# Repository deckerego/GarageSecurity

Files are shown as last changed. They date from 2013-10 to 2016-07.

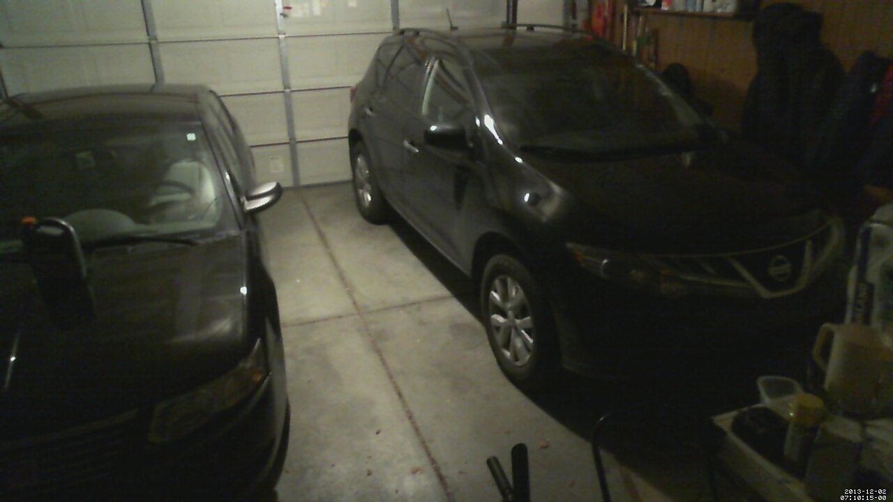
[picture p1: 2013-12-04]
app/test/unit/two_cars_closed_nightlight.jpg

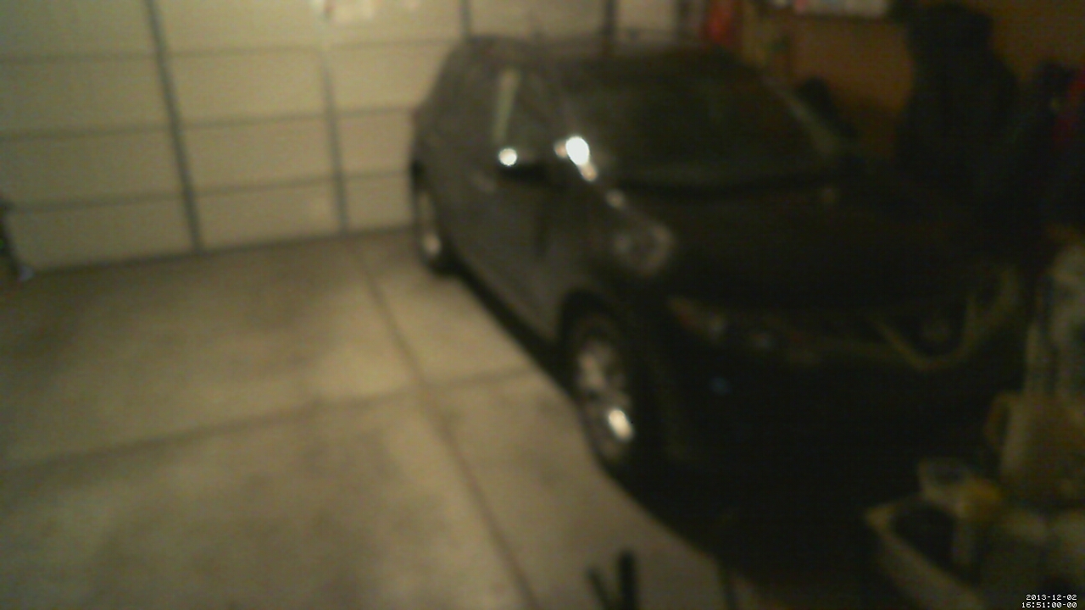
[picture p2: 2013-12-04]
app/test/unit/one_car_closed_nightlight.jpg

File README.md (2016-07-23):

GarageSecurity
==============

A web interface for remote residential garage surveillance. This uses a Raspberry Pi to connect to a universal garage door opener via GPIO and a webcam or Raspberry NoIR video camera.

Hardware Punch List
-------------------

<table>
  <tr>
    <td>Raspberry Pi (works with all models)</td>
    <td>https://www.adafruit.com/product/2266</td>
  </tr>
  <tr>
    <td>Raspberry Pi NoIR Camera (or a spare Video4Linux-compliant webcam)</td>
    <td>https://www.sparkfun.com/products/12654</td>
  </tr>
  <tr>
    <td>Chamberlain Universal Garage Remote</td>
    <td>http://www.chamberlain.com/clicker-and-accessories/universal-clicker-products/clicker-universal-remote-control</td>
  </tr>
  <tr>
    <td>Resistors, NPN transistors, NPN MOSFET</td>
    <td>Available at Sparkfun, Adafruit, Radio Shack or from de-soldering unused electronics.</td>
  </tr>
  <tr>
    <td>Optional: Honeywell Temperature and Humidity Sensor</td>
    <td>https://www.sparkfun.com/products/11295</td>
  </tr>
</table>

Security & OS Setup
-------------------

Ensure you install necessary updates and install a firewall (such as UFW) before proceeding. Rather than exposing motion and other services externally, we will be proxying them through Apache. This means the only ports you should need to open are port 80 (HTTP) and port 22 (SSH), especially since motion hasn't has as extensive vetting for security. As an example, you could setup a simple firewall as:
~~~~
sudo apt-get install ufw
sudo ufw allow 80
sudo ufw allow 22
sudo ufw enable
~~~~
Bear in mind GarageSec uses BASIC HTTP authentication and does not necessarily support SSL out of the box (although you could definitely add it), so man-in-the-middle interception of your password is super-de-duper possible.

Also - the latest version of Raspian (Jessie) doesn't bring up wireless interfaces on boot by default, even for the RPi 3. Which is odd. To fix this, make sure your wireless interfaces in `/etc/network/interfaces` are set to "auto," such as:
~~~~
auto wlan0
allow-hotplug wlan0
iface wlan0 inet manual
    wpa-conf /etc/wpa_supplicant/wpa_supplicant.conf
~~~~

It may be a good idea to create a crontab entry to delete old captured videos, e.g. `0 1 * * * find /home/motion -ctime +14 -delete`

To enable I2C communication for temperature and humidity monitoring, follow the I2C instructions from Adafruit available at https://learn.adafruit.com/adafruits-raspberry-pi-lesson-4-gpio-setup/configuring-i2c

Hardware Installation
---------------------

See http://hackaday.io/project/2049/instructions for hardware installation

Software Installation
---------------------

These installation instructions have been tested with the latest version of Raspian (Jessie)

1. Install the base packages with `sudo apt-get install wiringpi python-dev python-smbus python-imaging apache2 libapache2-mod-proxy-html libapache2-mod-authnz-external motion nodejs-legacy libav-tools npm monit`
2. Install Bower using `sudo npm install -g bower`
3. Enable the Apache2 modules using `sudo a2enmod authnz_external proxy_http`
4. If you are using the Raspberry Pi camera, add `bcm2835-v4l2` to /etc/modules
5. Edit `/etc/default/motion` and set it to start on boot
6. Clone this repository or download https://github.com/deckerego/GarageSecurity/archive/master.zip which will include the Bottle webapp and some admin configs/scripts
7. Install GarageSecurity's dependencies using `sudo pip install -r app/requirements.txt`
8. Expose any GPIO ports you connect the garage door opener or light switches using the WiringPi GPIO Utility, e.g. `gpio export 17 out`. You may want to add this statement to `/etc/rc.local` so that it will be exported at startup. A sample rc.local is provided.
9. Allow the pi user to access motion files by adding it to the `motion` user group in /etc/group
10. Copy the files within the app/ directory into /srv/garagesec
11. Change into the /srv/garagesec/views directory and execute `bower install bootstrap`
12. Copy the service config files from config/etc into the appropriate /etc directory, altering them as needed.
13. Copy the alert scripts from the `scripts/` directory into `/usr/local/motion`, modifying `rest_call.sh` so that API_USER and API_PASS are set to your "pi" usernamed and password used to log in to Apache
14. Create a copy of app/config.sample as /srv/garagesec/config.py, altering config.py to fit your preferences
15. Enable the webapp with `sudo a2dissite 000-default`, followed by `sudo a2ensite security`, then start up (or restart) Apache2
16. Ensure config/etc/init.d/garagesec has been copied to /etc/init.d, then install it using `sudo update-rc.d garagesec defaults`
17. Start the webapp using `sudo service garagesec start`

GPIO Permissions Issues
-----------------------
You may find that the GPIO buttons don't work as expected - this may be due to permissions issues within the `/sys/class/gpio/` devices. This can sometimes be fixed by changing `/etc/udev/rules.d/99-com.rules` to have the following gpio rules: `SUBSYSTEM=="gpio*", PROGRAM="/bin/sh -c 'chown -H -R root:gpio /sys/class/gpio/* && chmod -R 770 /sys/class/gpio/*; chown -R root:gpio /sys/devices/virtual/gpio && chmod -R 770 /sys/devices/virtual/gpio'"`

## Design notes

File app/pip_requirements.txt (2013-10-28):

bottle==0.11.6
nose>=1.1.2
flexmock==0.9.7
wiringpi>=1.0.5

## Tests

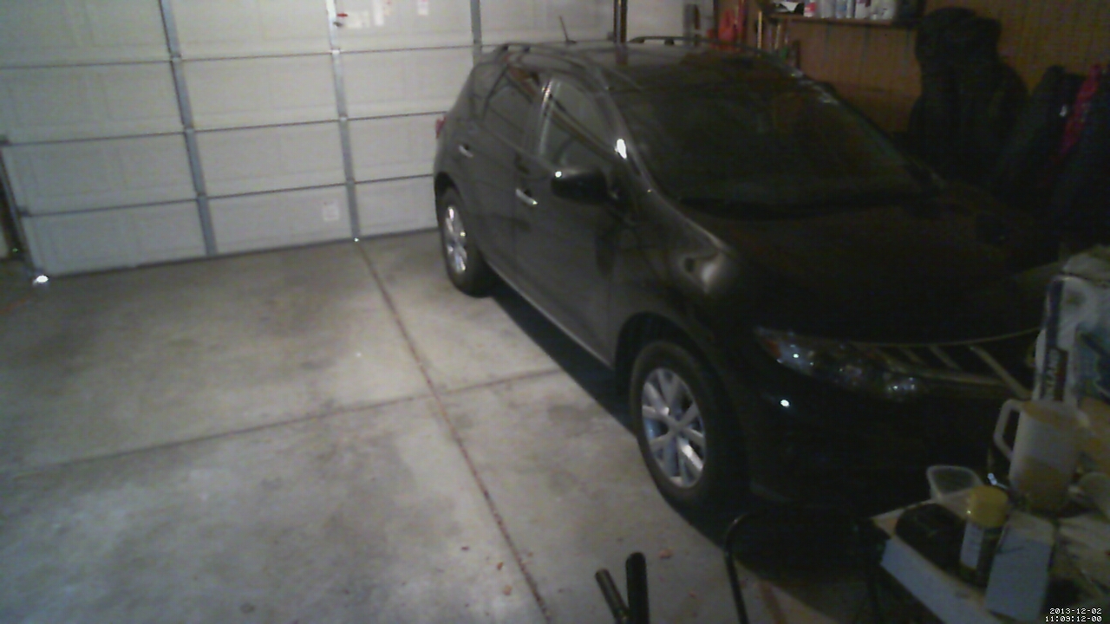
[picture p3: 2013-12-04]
app/test/unit/one_car_closed_day.jpg

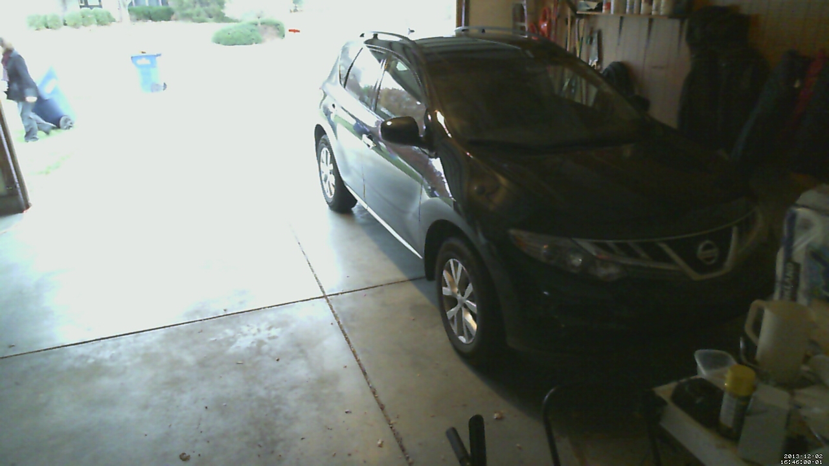
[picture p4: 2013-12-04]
app/test/unit/one_car_open_day.jpg

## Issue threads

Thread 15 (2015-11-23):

2 door setup

kfakhri1, 2015-11-23:
Hi, thanks for posting this, any way this could be configured for two door garages?  As in left door and right door?  Thank you.

deckerego, 2016-04-20:
Yup, that's a doable thing - will look into that.

DervMan, 2016-04-21:
As a variation to that, my door uses a separate button for open and close so I also need two buttons but for a slightly different reason!

DervMan, 2017-01-18:
I've treid to add a second button, in my case I'm after an 'Open' and 'Close'. Although the code below adds the button clicking the new button results in the 'Open button' relay being operated.  Assuming I need to update some more code by struggling to see where.

`<li><button type="button" id="openDoor" class="btn btn-default navbar-btn" onClick="executeCommand();">Open</button></li>
					<li><button type="button" id="closeDoor" class="btn btn-default navbar-btn" onClick="executeCommand();">Close</button></li>`

deckerego, 2017-01-19:
You would need two different JavaScript functions to call - one to open, another to close. Take a look at `events.js` - it has a function called `executeCommand()` that calls `remote/0`. To add a second button, you would need:
1. A new REST endpoint like `remote/` that would trigger a new GPIO pin
2. A new JavaScript function that called this REST endpoint
3. The new button on the UI

deckerego, 2017-01-20:
@DervMan and @kfakhri1 - long at last I have a test out that you guys might try. I've labelled two buttons "Open/Close Door #1" and "Open/Close Door #2," but those are temporary labels for now. This _should_ allow you to fire two different buttons: one on GPIO #17, the other on GPIO #27.

You may even want to just fork the branch `double_button` - if it doesn't work, it should be pretty dang close. Let me know if either of you have success!

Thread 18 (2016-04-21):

Camera0 URL on main page is a static URL

DervMan, 2016-04-21:
When accessing GarageSec main page on anything other than port 80 the camera stream is broken. This link needs to be created dynamically so TCP port changes don't break the URL.

		<script src="installed/jquery/dist/jquery.min.js"></script>
		<script src="installed/bootstrap/dist/js/bootstrap.min.js"></script>
		<script type="text/javascript" src="js/mjpeg_viewer.js"></script>
		<script type="text/javascript" src="js/events.js"></script>
		<script type="text/javascript">
			loadThermals("temperature", "humidity")
			renderCamera("camera0", "http://10.10.10.10/camera0");
			silenceStatus("silent");
			lastEvent("lastevent")
		</script>

deckerego, 2016-07-19:
Implemented as a config change

Closed 2016-07-19.

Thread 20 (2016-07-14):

GarageSecurity not starting up -

DervMan, 2016-07-14:
When trying to open the door I'm seeing a wiringpi GPIO error. Version  WebIOPi-0.7.1.

`root@raspberrypi:/srv/garagesec# python run_server.py
Bottle v0.12.9 server starting up (using WSGIRefServer())...
Listening on http://localhost:9003/
Hit Ctrl-C to quit.

127.0.0.1 - - [14/Jul/2016 12:33:12] "GET / HTTP/1.1" 200 2229
127.0.0.1 - - [14/Jul/2016 12:33:14] "GET /installed/bootstrap/dist/css/bootstrap.min.css HTTP/1.1" 304 0
127.0.0.1 - - [14/Jul/2016 12:33:14] "GET /installed/bootstrap/dist/js/bootstrap.min.js HTTP/1.1" 304 0
127.0.0.1 - - [14/Jul/2016 12:33:14] "GET /installed/jquery/dist/jquery.min.js HTTP/1.1" 304 0
127.0.0.1 - - [14/Jul/2016 12:33:14] "GET /css/styles.css HTTP/1.1" 304 0
127.0.0.1 - - [14/Jul/2016 12:33:14] "GET /js/mjpeg_viewer.js HTTP/1.1" 304 0
127.0.0.1 - - [14/Jul/2016 12:33:14] "GET /installed/bootstrap/dist/css/bootstrap-theme.min.css HTTP/1.1" 304 0
127.0.0.1 - - [14/Jul/2016 12:33:15] "GET /js/events.js HTTP/1.1" 304 0
Traceback (most recent call last):
  File "/usr/local/lib/python2.7/dist-packages/bottle.py", line 862, in _handle
    return route.call(**args)
  File "/usr/local/lib/python2.7/dist-packages/bottle.py", line 1732, in wrapper
    rv = callback(*a, **ka)
  File "/srv/garagesec/HIH6130.py", line 53, in wrapper
    rv = callback(*args, **kwargs)
  File "/srv/garagesec/routes.py", line 86, in get_environment
    humidity, celsius, status = temperature.get_conditions()
  File "/srv/garagesec/HIH6130.py", line 65, in get_conditions
    self.bus.write_quick(self.address)
IOError: [Errno 110] Connection timed out
127.0.0.1 - - [14/Jul/2016 12:33:18] "GET /environment HTTP/1.1" 500 751
Traceback (most recent call last):
  File "/usr/local/lib/python2.7/dist-packages/bottle.py", line 862, in _handle
    return route.call(**args)
  File "/usr/local/lib/python2.7/dist-packages/bottle.py", line 1732, in wrapper
    rv = callback(*a, **ka)
TypeError: get_lastevent() takes exactly 1 argument (0 given)
127.0.0.1 - - [14/Jul/2016 12:33:18] "GET /lastevent HTTP/1.1" 500 749
Traceback (most recent call last):
  File "/usr/local/lib/python2.7/dist-packages/bottle.py", line 862, in _handle
    return route.call(**args)
  File "/usr/local/lib/python2.7/dist-packages/bottle.py", line 1732, in wrapper
    rv = callback(*a, **ka)
TypeError: get_silence() takes exactly 1 argument (0 given)
127.0.0.1 - - [14/Jul/2016 12:33:18] "GET /alerts HTTP/1.1" 500 746
Traceback (most recent call last):
  File "/usr/local/lib/python2.7/dist-packages/bottle.py", line 862, in _handle
    return route.call(**args)
  File "/usr/local/lib/python2.7/dist-packages/bottle.py", line 1732, in wrapper
    rv = callback(*a, **ka)
  File "/srv/garagesec/routes.py", line 149, in read_light_switch
    state = "true" if gpio.read_switch(switch) else "false"
  File "/srv/garagesec/gpio.py", line 38, in read_switch
    **io = wiringpi.GPIO(wiringpi.GPIO.WPI_MODE_SYS)**
AttributeError: type object 'GPIO' has no attribute 'WPI_MODE_SYS'
127.0.0.1 - - [14/Jul/2016 12:33:18] "GET /light/0 HTTP/1.1" 500 747
127.0.0.1 - - [14/Jul/2016 12:33:18] "GET /favicon.ico HTTP/1.1" 200 2686

`

deckerego, 2016-07-19:
Will work on converting the project to the latest build of Raspian

deckerego, 2016-07-22:
I was unable to reproduce on a brand-new build from master using the latest from Raspian. Can you confirm you are running the latest?

Closed 2016-07-23.

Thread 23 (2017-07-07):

Service Unavailable

wjstone, 2017-07-07:
I've tried installing several times and keep ending up getting
"Service Unavailable

The server is temporarily unable to service your request due to maintenance downtime or capacity problems. Please try again later."

any ideas what might be causing it?

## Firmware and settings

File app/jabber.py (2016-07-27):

import sleekxmpp
import inspect
import logging
import datetime
import os, time
from s3 import S3
from camera import Camera
from config import configuration

logger = logging.getLogger('garagesec')
logger.setLevel(20)

class Jabber(sleekxmpp.ClientXMPP):
  name = 'jabber_xmpp'
  keyword = 'jabber'

  def __init__(self, jid, password, camera, temperature):
    super(Jabber, self).__init__(jid, password)

    self.camera = camera
    self.temperature = temperature
    self.instance_name = configuration.get('instance_name').lower()
    self.silent = True

    if jid and password:
        self.silent = False
        self.add_event_handler('session_start', self.start, threaded=False, disposable=True)
        self.add_event_handler('message', self.receive, threaded=True, disposable=False)

  def __del__(self):
    self.close()

  # This is invoked when installed as a Bottle plugin
  def setup(self, app):
    self.routes = app

    for other in app.plugins:
      if not isinstance(other, Jabber):
        continue
      if other.keyword == self.keyword:
        raise PluginError("Found another instance of Jabber running!")

    host = configuration.get('xmpp_server_host')
    port = configuration.get('xmpp_server_port')

    if not host or not port:
        logger.warn("No XMPP settings defined, disabling Jabber")
    else:
        if self.connect((host, port)):
          logger.info("Opened XMPP Connection")
          self.process(block=False)
        else:
          raise Exception("Unable to connect to Google Jabber server")

        self.bucket = S3()

  # This is invoked within Bottle as part of each route when installed
  def apply(self, callback, context):
    conf = context.config.get('jabber') or {}
    keyword = conf.get('keyword', self.keyword)

    args = inspect.getargspec(context.callback)[0]
    if keyword not in args:
      return callback

    def wrapper(*args, **kwargs):
      kwargs[self.keyword] = self
      rv = callback(*args, **kwargs)
      return rv
    return wrapper

  # De-installation from Bottle as a plugin
  def close(self):
    logger.info("Closing XMPP Connection")
    self.disconnect(wait=False)

  def start(self, event):
    self.send_presence()
    self.get_roster()

  def send_alert_image(self, file_path):
    if not self.silent:
      file_bin = open(file_path, 'r').read()
      file_url = self.bucket.upload(file_bin)
      self.send_alert_msg(file_url)

  def send_alert_msg(self, body):
    if not self.silent:
        for recipient in configuration.get('xmpp_recipients'):
          message = self.Message()
          message['to'] = recipient
          message['type'] = 'chat'
          message['body'] = body

          logger.debug("Sending message: %s" % message)
          message.send()

  def set_silence(self, silent):
      self.silent = silent

  def receive(self, message):
    if message['type'] in ('chat', 'normal'):
      logger.debug("XMPP Message: %s" % message)
      from_account = "%s@%s" % (message['from'].user, message['from'].domain)
      logger.info("Received message from %s" % from_account)

      if not from_account in configuration.get('xmpp_recipients'):
        logger.warn("Received message from non-whitelist user %s: %s" % (from_account, message['body']))
      elif "%s camera" % self.instance_name in message['body'].lower():
        image_bin = self.camera.get_image()
        image_url = self.bucket.upload(image_bin)
        message.reply("Status: %s" % image_url).send()
      elif "%s lastevent" % self.instance_name in message['body'].lower():
        archive_dir = configuration.get('webcam_archive')
        time_struct = max(map(lambda x: os.path.getmtime("%s/%s" % (archive_dir, x)), os.listdir(archive_dir)))
        message.reply("Last Event: %s" % time.strftime("%c", time.localtime(time_struct))).send()
      elif "%s climate" % self.instance_name in message['body'].lower():
        humidity, celsius, status = self.temperature.get_conditions()
        farenheit = ((celsius * 9) / 5) + 32
        message.reply("Temperature: %0.2fF, Humidity: %0.2f%%" % (farenheit, humidity)).send()
      elif "%s silent" % self.instance_name in message['body'].lower():
        self.silent = True
        message.reply("Silencing alerts").send()
      elif "%s audible" % self.instance_name in message['body'].lower():
        self.silent = False
        message.reply("Enabling alerts").send()
      else:
        logger.info("Uncaught command from %s: %s" % (from_account, message['body']))

class PluginError(Exception):
  pass

Plugin = Jabber

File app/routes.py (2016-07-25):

#!/usr/bin/env python
# -*- coding: utf-8 -*-

import os, sys
import logging

logging.basicConfig(level=logging.WARN, format='%(levelname)-8s %(message)s')
logger = logging.getLogger('garagesec')

os.chdir(os.path.dirname(__file__))
sys.path.insert(0, os.path.abspath(os.path.join(os.path.dirname(__file__), ".")))

import json
import time, datetime
import re
from piwiring import GPIO
from jabber import Jabber
from camera import Camera
from HIH6130 import Temperature
from media import Media
from config import configuration
from bottle import Bottle, HTTPResponse, static_file, get, put, request, response, template, redirect

instance_name = configuration.get('instance_name')

camera = Camera()
temperature = Temperature()
gpio = GPIO()
jabber_service = Jabber(configuration.get('xmpp_username'), configuration.get('xmpp_password'), camera, temperature)
media = Media()

application = Bottle()
application.install(temperature)
application.install(gpio)
application.install(jabber_service)
application.install(media)

@application.route('/favicon.ico')
def send_favicon():
	return static_file('favicon.ico', root='views/images')

@application.route('/installed/<filename:path>')
def send_bower(filename):
	return static_file(filename, root='views/bower_components')

@application.route('/js/<filename:path>')
def send_js(filename):
	return static_file(filename, root='views/js')

@application.route('/css/<filename:path>')
def send_css(filename):
	return static_file(filename, root='views/css')

@application.get('/')
def index():
	return home()

@application.get('/home')
def home():
	return template('index', webcam_url=configuration.get('webcam_url'))

@application.get('/archive')
def archive(media):
	archive_dates = media.get_dates()
	archive_date = request.query.date
	if not (archive_date and media.is_valid_date(archive_date)):
		archive_date = archive_dates[0]

	image_files = media.get_files(archive_date)
	return template('media', images=image_files, date=archive_date, dates=archive_dates)

@application.get('/video')
def video(media):
	video_file = request.query.vid
	archive_date = request.query.date

	if (not media.is_valid_date(archive_date)) or (not media.is_valid_video(video_file)):
		return archive(media)

	return template('video', archive_video=video_file, date=archive_date)

@application.get('/status')
def show_status():
	archive_dir = configuration.get('webcam_archive')
	archive_dir = configuration.get('webcam_archive')
	time_struct = max(map(lambda x: os.path.getmtime("%s/%s" % (archive_dir, x)), os.listdir(archive_dir)))
	return '{ "last_area_detected": "%s" }' % time.strftime("%c", time.localtime(time_struct))

@application.get('/environment')
def get_environment(temperature):
	humidity, celsius, status = temperature.get_conditions()
	fahrenheit_val = ((celsius * 9) / 5) + 32 if celsius else "null"
	celsius_val = celsius if celsius else "null"
	humidity_val = humidity if humidity else "null"
	status_val = status if status else "null"
	return '{ "relative_humidity": %s, "celsius": %s, "fahrenheit": %s, "status": %s }' % (humidity_val, celsius_val, fahrenheit_val, status_val)

@application.get('/snapshot')
def show_snapshot():
	response.headers['Content-Type'] = 'image/jpeg'
	return camera.get_image()

@application.put('/picture_save')
def picture_save(jabber, media):
	motion_event = request.json
	image_file_path = motion_event['file']
	image_file_dir = os.path.dirname(image_file_path)

	jabber.send_alert_image(image_file_path)

	if image_file_dir.index(configuration.get('webcam_archive')) == 0:
		media.save_thumbnail(image_file_path)

	return request.body.getvalue()

@application.put('/movie_start')
def movie_start():
	return request.body.getvalue()

@application.put('/movie_end')
def movie_end(media):
	motion_event = request.json
	video_file_path = motion_event['file']
	video_file_dir = os.path.dirname(video_file_path)

	if video_file_dir.index(configuration.get('webcam_archive')) == 0:
		media.transcode(video_file_path)

	return request.body.getvalue()

@application.put('/motion_detected')
def motion_detected():
	return request.body.getvalue()

@application.put('/area_detected')
def area_detected(jabber):
	motion_event = request.json
	date_time = time.localtime(motion_event['event_time'])
	time_string = time.strftime('%a, %d %b %Y %H:%M:%S', date_time)

	jabber.send_alert_msg('Motion in %s Detected at %s' % (instance_name, time_string))

	return request.body.getvalue()

@application.put('/remote/<button:int>')
def push_remote_button(button, gpio):
	if gpio.push_button(button):
		return '{ "pressed": %d }' % button
	else:
		raise HTTPResponse('{ "error": %d }' % button, 500)

@application.get('/light/<switch:int>')
def read_light_switch(switch, gpio):
	state = "true" if gpio.read_switch(switch) else "false"
	return '{ "enabled": %s }' % state

@application.put('/light/<switch:int>')
def flip_light_switch(switch, gpio):
	if gpio.flip_switch(switch):
		return '{ "flipped": %d }' % switch
	else:
		raise HTTPResponse('{ "error": %d }' % switch, 500)

@application.get('/lastevent')
def get_lastevent(jabber):
	archive_dir = configuration.get('webcam_archive')
	time_struct = max(map(lambda x: os.path.getmtime("%s/%s" % (archive_dir, x)), os.listdir(archive_dir)))
	return '{ "datetime": "%s" }' % time.strftime("%c", time.localtime(time_struct))

@application.get('/alerts')
def get_silence(jabber):
	return '{ "silence": %s }' % ("true" if jabber.silent else "false")

@application.put('/alerts')
def set_silence(jabber):
	silence_request = request.json
	jabber.set_silence(silence_request['silence'])
	return get_silence(jabber)

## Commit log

2013-10-26 Fire the GPIO pin for the door remote
2013-10-30 Switched to Skeleton CSS for reactive design
2013-10-30 Revert "Switched to Skeleton CSS for reactive design"
    This reverts commit 14dd4567be4e7c3347d3f2648352f98507370559.
    [routes.py]
2013-11-27 Issue #3 Issue #4 - Initial addition of XMPP for notifications; REST exposure
    [jabber.py, routes.py]
2013-11-27 Issue #3 - Implemented XMPP messages
    [jabber.py, routes.py]
2013-12-10 Fixed typo in last event date
    [jabber.py, routes.py]
2014-09-05 Better Jabber integration, error handlng improvements
    [jabber.py, routes.py]
2014-12-28 Added in temperature/humidity support via HIH6130
2014-12-29 Fixed typos for lastevent
    [jabber.py]
2015-01-13 Continue bravely on if I2C does not work
    [HIH6130.py]
2015-01-23 Safe failure when i2c fails
    [HIH6130.py, routes.py]
2015-08-15 Additional Monit configs, cleanup, added wiring diagram for GPIO switches
    [GPIO Switches.fzz]
2015-08-22 Cleanup and path fixes
    Relative pathing and bug fixes
    [GPIO Switches.fzz]
2015-09-05 Documentation Cleanup
    Added Bootstrap installation and removed extraneous Camera reference in
    Jabber
2015-09-07 Jabber cleanup
    Cleanup of Jabber threading
2015-09-21 Video archive page
    more-or-less completed video archive page that doesn’t require Apache
    indexes
    [media.py, routes.py]
2015-09-22 Removed index pages, fixed thumbnail sorting
    Removed index pages for GarageSec media since it’s native to the app
    now; fixed thumbnail sorting
    [media.py]
2015-10-12 Re-add webm transcoding
    So it turns out that the extpipe option of motion causes /dev/video0 to
    completely bug out (it doesn’t like the concurrent access), and Vorbis
    support isn’t there yet. Falling back to transcoding.
    [media.py, routes.py]
2016-06-16 Added ability to flip on/off lights
    [routes.py]
2016-07-23 Initial round of bug fixes reported by DervMan
    [jabber.py]
2016-07-23 Migrated to WiringPi2
2016-07-23 Fail silently if temp/humidity sensor is not attached
    [HIH6130.py]
2016-07-25 Create a stateful class for lazy-init of wiringpi
2016-07-27 Fixed bad init when Jabber was missing
    [jabber.py]
2017-01-20 Added additional garage door button for Issue #15
    [piwiring.py]
